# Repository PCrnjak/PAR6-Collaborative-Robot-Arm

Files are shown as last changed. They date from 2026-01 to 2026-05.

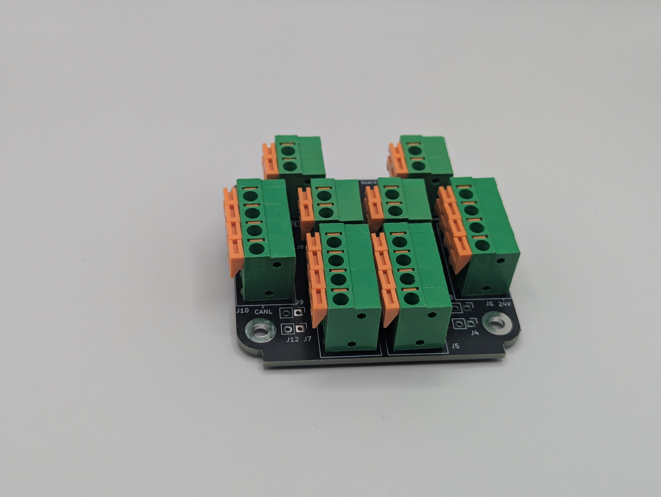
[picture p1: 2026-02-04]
BOM/BOM reference images/Base Distribution board.jpg

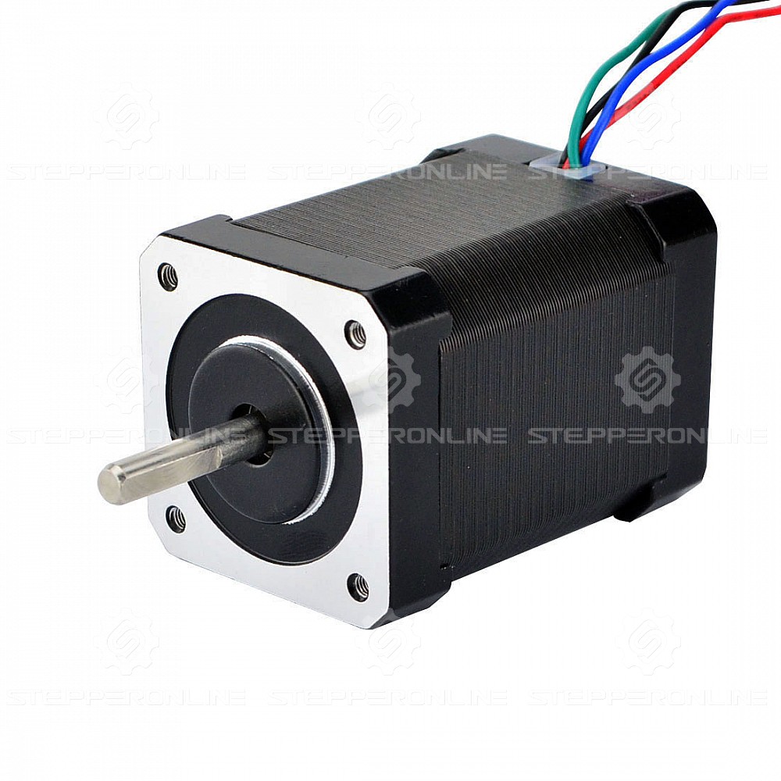
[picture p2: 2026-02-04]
BOM/BOM reference images/stepper 60mm.jpg

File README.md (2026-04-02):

> [!CAUTION]
> This is a BETA release: Instructions, code, and 3D print files may change in the future and are not yet finalized.

By building and using this system, you acknowledge that it is still under active development and may contain errors, incomplete features, or design issues. You are doing so entirely at your own risk and responsibility.

This project may require troubleshooting, modifications, and technical knowledge. Proceed only if you are comfortable working with electronics, mechanical systems, and software in a development-stage environment.
>

## 🐞 Beta Feedback

Since this project is currently in beta, feedback is highly appreciated.

If you find any mistakes, bugs, or unclear parts, please report them, including issues in:

- Documentation
- BOM and assembly documentation
- Source code
- STL and other 3D print files

Please open an issue, send us a message on Discord, or contact us via email with as much detail as possible so we can fix it quickly.

<div align="center">



# PAR6-Collaborative-Robot-Arm

</div>

---

<p align="center">
  
  
  
  <a href="https://github.com/petercorke/robotics-toolbox-python">Powered by the Robotics Toolbox</a>
  
</p>

<p align="center">
  
  
  
  
  
  
</p>

<div align="center">

3D Printed Collaborative Robot - Open Source Software, Manuals & 3D print files ·

Designed for Embodied/Physical  AI, Safety & Ease of use

</div>

## 💡 News

[2025-04-10] Test

[2025-04-03] Beta Release! Contributions from the open-source community are highly encouraged, and we welcome feedback and bug reports through the GitHub Issues page.

## 📖 Project Overview

PAR6 is a 3D-printed collaborative robot arm platform designed for research, education, and rapid prototyping in physical AI.

The project combines mechanical design files, assembly documentation, and software resources to support full-stack robotics development.

Key focus areas:

- Embodied AI and physical AI experiments and validation
- Teleoperation workflows and human-in-the-loop control
- Learning from demonstration (LfD) pipelines
- Imitation learning and dataset generation
- VLA-style data collection for AI-native robotics
- Accessible robotics research through open hardware and open documentation

## ⚒️How to build / Where to buy?

## 📚Documentation:

| Resource | Description |
|---|---|
| [3D Print Files](3D%20Print%20Files/) | Printable STL part files for the PAR6 robot arm,  |
| [BOM](BOM/) | Bill of materials and reference images for sourcing the required parts |
| [Building Instructions](Building%20Instructions/) | Assembly notes, cable building instructions, and supporting datasheets |
| [PAR6 Description](PAR6%20Description/) |  XML files, and URDF resources for simulation  |

## ⚙️ Hardware Specifications

## 🗺️ Roadmap & Status

Schedule:

| Task | Status | Description | Documentation |ETA |
| :--- | :---: | :--- | :--- | :--- |
| dsa | sad | sad | asd | asd |
---

## 🤝Get Involved

## 🌐 More about PAR6 robotic arm

| YouTube | Instagram | Twitter | LinkedIn |
|---|---|---|---|
|  |  |  |  |

| Discord | Forum | Hackaday | Blog |
|---|---|---| ---|
|  |  |  |  

## 🛡️ Licensing

CERN Open Hardware Licence Version 2 - Strongly Reciprocal

## 💸Support us

The majority of this project is open source and freely available to everyone. Your assistance, whether through donations or advice, is highly valued. Thank you!

 


## 🙌 References & Acknowledgments

## ⚠️ Safety, Liability & Disclaimer
This project includes experimental software, hardware designs, and assembly documentation that are still under development and may contain bugs, errors, or incomplete features. By using, building, or modifying this project, you acknowledge that:

* You use this project entirely at your own risk
* You are solely responsible for safe assembly, testing, and operation
* No guarantee is made regarding correctness, safety, or reliability
* The authors are not responsible for any damage, injury, or loss resulting from the use or misuse of this project
* Hardware performance and safety depend on user assembly, component quality, calibration, and handling, which cannot be guaranteed
* This project is provided “as is.” If you choose to build a device yourself using these files, designs, or instructions, you do so without any warranties or guarantees, including regarding safety, reliability, or suitability for any particular purpose.

THIS PROJECT INVOLVES LETHAL VOLTAGES AND OTHER SERIOUS HAZARDS THAT CAN CAUSE SEVERE INJURY. YOU MUST READ THE FULL [SAFETY WARNING AND DISCLAIMER DOCUMENT](SAFETY_WARNING_AND_DISCLAIMER.md)  BEFORE USING ANY PROJECT FILES. BY PROCEEDING, YOU ACKNOWLEDGE AND ACCEPT ALL RISKS AND AGREE TO USE THIS PROJECT ENTIRELY AT YOUR OWN RESPONSIBILITY.

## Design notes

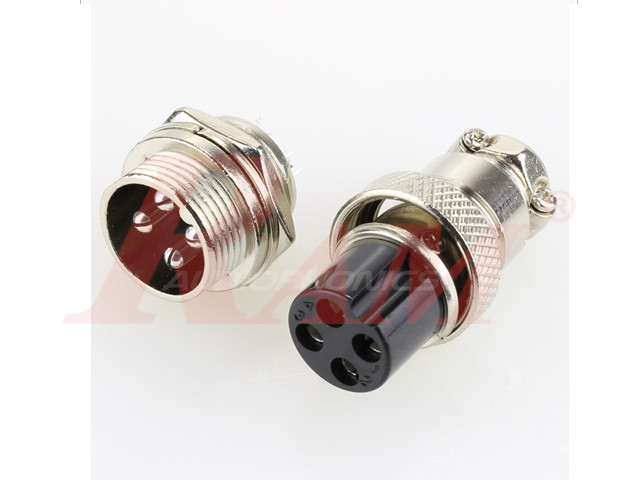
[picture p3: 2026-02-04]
BOM/BOM reference images/GX16-4 Pole Metal Male Female Panel Chassis Connector.jpg

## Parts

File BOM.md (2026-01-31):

# Gripper – Bill of Materials (BOM)

This BOM lists all components required to build the gripper. Quantities are for **one gripper**.

---

## Screws and Nuts

| Diameter / Type | Length | Quantity | Description | Link |
|---|---|---|---|---|
| M3 | 22 mm | 4 | Screw |  |
| M4 | 10 mm | 2 | Screw |  |
| M3 | 6 mm | 4 | Cheese head screw |  |
| M3 | 25 mm | 4 | Screw |  |
| M3 | 8 mm | 6 | Screw |  |
| M2 | 10 mm | 1 | Screw |  |
| M2 | 4 mm | 8 | Screw |  |
| M2.5 | 8 mm | 6 | Screw |  |
| M2 | 6 mm | 4 | Screw |  |
| M3 | 40 mm | 4 | For 17HS16-2004S1 stepper |  |
| M3 | 60 mm | 4 | For 17HS24-2104S stepper |  |

---

## Brass Inserts

| Thread | Length | Outer Diameter | Quantity | Link |
|---|---|---|---|---|
| M3 | 5 mm | 4.5 mm | 8 | [Link](https://s.click.aliexpress.com/e/_c2RX6lzp) |

---

## Motors (You need one of these per gripper!)

| Type | Quantity | Description | Link |
|---|---|---|---|
| 17HS08-1004S | 1 | 21.5mm stepper | [Link](https://www.omc-stepperonline.com/nema-17-bipolar-1-8deg-16ncm-22-6oz-in-1a-3-7v-42x42x20mm-4-wires-17hs08-1004s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)  |
| 17HS16-2004S1 | 1 | 40mm stepper  | [Link](https://www.omc-stepperonline.com/nema-17-bipolar-45ncm-64oz-in-2a-42x42x40mm-4-wires-w-1m-cable-connector-17hs16-2004s1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) |
| 17HS24-2104S | 1 | 60mm stepper | [Link](https://www.omc-stepperonline.com/nema-17-bipolar-1-8deg-65ncm-92oz-in-2-1a-3-36v-42x42x60mm-4-wires-17hs24-2104s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) |

---

## Mechanical Components

| Type | Quantity | Description | Link |
|---|---|---|---|
| Shaft coupler | 1 | 8 mm bore, M4 screw holes | [Link](https://s.click.aliexpress.com/e/_c3pkoqsb) |
| MGN7C slider | 2 | Linear guide carriage | [Link](https://s.click.aliexpress.com/e/_c4sRNxXV) |
| Linear guide | 1 | 100 mm, 150 mm and 200 length works | [Link](https://s.click.aliexpress.com/e/_c4sRNxXV) |
| Magnet | 1 | 6 mm diameter, 2.5 mm thickness | [Link](https://source-robotics.com/products/6x2-5mm-diametrical-neodymium-magnet) |
| Gear 32P 21T | 1 | | [Link](https://s.click.aliexpress.com/e/_c3oAnoc7) |
| Thermal cement | 1 | | [Link](https://s.click.aliexpress.com/e/_c3dBOwTD) |

---

## Electronics

| Type | Quantity | Description | Link |
|---|---|---|---|
| STEPFOC motor controller | 1 | Motor controller | [Link](https://source-robotics.com/products/spectral-micro-bldc-controller) |
| 100K Thermistor | 1 | NTC temperature sensor | [Link](https://source-robotics.com/products/100k-ntc-thermistor) |
| XH 2.54 mm cable | 1 | 300 mm, 2P, double-ended (24 V power) | [Link](https://s.click.aliexpress.com/e/_c3f1efET) |
| ZH 1.5 mm cable | 1 | 300 mm, 2P, double-ended (CAN bus) | [Link](https://s.click.aliexpress.com/e/_c3f1efET)  |
| Male 4-pin connector | 1 | Board connector | [Link](https://s.click.aliexpress.com/e/_c4OWHPKF) |
| OV9732 Camera | 1 | 100 Degree version | [Link](https://s.click.aliexpress.com/e/_c3WWVLjl) |

---

## Cables
Official cables from Source Robotics: [Link]()

Diy version below:

| Type | Length / Spec | Quantity | Description | Link |
|---|---|---|---|---|
| 26 AWG cable | 0.15 mm², 4-wire twisted pair | 0.4 m | ~40 cm usually sufficient | [Link](https://s.click.aliexpress.com/e/_c4m3ggwn) |
| 4-pin male wire connector | — | 1 | See reference image |[Link](https://s.click.aliexpress.com/e/_c4OWHPKF) |
| 4-pin female wire connector | — | 1 | See reference image | [Link](https://s.click.aliexpress.com/e/_c4OWHPKF) |

---

---

> **Note:** Equivalent parts from other suppliers may be used as long as specifications match.

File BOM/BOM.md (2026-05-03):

# PAROL6 – Bill of Materials (BOM)

This BOM lists all components required to build the PAR6 robot arm based on the official kiting list.

---

## RCB - Robot Control Box

TODO - Check this repository to build your Robot Control Box

---

## Screws and Nuts

| Diameter / Type | Length | Quantity | Description |
| :--- | :--- | :--- | :--- |
| M4 | 10 mm | 7 | DIN 912 / ISO 4762 (Socket head cap) 
| M3 | 8 mm | 50 | DIN 912 / ISO 4762 (Socket head cap) 
| M3 | 14 mm | 33 | DIN 912 / ISO 4762 (Socket head cap) 
| M3 | 25 mm | 4 | DIN 912 / ISO 4762 (Socket head cap) 
| M2 | 10 mm | 2 | DIN 912 / ISO 4762 (Socket head cap) 
| M2 | 4 mm | 2 | DIN 912 / ISO 4762 (Socket head cap) 
 M3 | 45 mm | 6 | DIN 912 / ISO 4762 (Socket head cap) 
  M2.5 | 14 mm | 8 | DIN 912 / ISO 4762 (Socket head cap) 
| M3 | 16 mm | 6 | DIN 912 / ISO 4762 (Socket head cap) 
| M3 | 12 mm | 3 | DIN 912 / ISO 4762 (Socket head cap) 
| M4 | 16 mm | 16 | DIN 912 / ISO 4762 (Socket head cap) 
| M4 | 14 mm | 4 | DIN 912 / ISO 4762 (Socket head cap)
| M4 | 50 mm | 4 | DIN 912 / ISO 4762 (Socket head cap)
| M3 | 15 mm or 16 | 5 | Tapered / Countersunk screw head 
| M5 | 16 mm | 8 | DIN 912 / ISO 4762 (Socket head cap)|
| M3 | 22 mm | 4 | DIN 912 / ISO 4762 (Socket head cap)|
| M3 | 40 mm | 8 | DIN 912 / ISO 4762 (Socket head cap)| 
| M3| 60 mm | 12 | DIN 912 / ISO 4762 (Socket head cap)| 

---

[Alt Link](https://s.click.aliexpress.com/e/_oEhMNU5)

## Gearboxes

| Name | Type | Quantity | Description | Link | ALT link| Reference Image |
| :--- | :--- | :--- | :--- | :--- | :--- |:--- |
| Gearbox 20:1 | Nema 17 20:1 | 2 | EG Series precision planetary | [Link](https://www.omc-stepperonline.com/eg-series-planetary-gearbox-gear-ratio-20-1-backlash-20-arc-min-for-nema-17-stepper-motor-eg17-g20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) | [Alt Link](https://s.click.aliexpress.com/e/_oEhMNU5) | [Link](BOM%20reference%20images/stepper%2020_1.jpg) |
| Gearbox 10:1 | Nema 17 10:1 | 1 | EG Series precision planetary | [Link](https://www.omc-stepperonline.com/eg-series-planetary-gearbox-gear-ratio-10-1-backlash-15-arc-min-for-nema-17-stepper-motor-eg17-g10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) | [Alt Link](https://s.click.aliexpress.com/e/_oEhMNU5) |[Link](BOM%20reference%20images/stepper%2010_1.jpg) |
| Gearbox 25:1 | Nema 17 10:1 | 1 | MGL Series precision planetary | [Link](https://www.omc-stepperonline.com/mgl-series-planetary-gearbox-gear-ratio-25-1-backlash-45arc-min-for-5mm-shaft-standard-nema-17-stepper-motor-mgl17-g25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) | [Alt Link](https://s.click.aliexpress.com/e/_c2QcIBnD) |[Link](BOM%20reference%20images/stepper%2010_1.jpg) |

25:1 Gearbox is still being tested. It might replace 20:1 used in J2!

> [!NOTE]
>     **You can use Lower quality MSG type reducers. They offer a tradeoff where they are cheaper but have more backlash**

---

## Motors

| Name | Type | Quantity | Description | Link | ALT link| Reference Image |
| :--- | :--- | :--- | :--- | :--- | :--- | :--- |
| Stepper 17HS08-1004S | Nema 17 | 1 | 16Ncm, 42x42x21.5mm; used in J6| [Link](https://www.omc-stepperonline.com/nema-17-bipolar-1-8deg-16ncm-22-6oz-in-1a-3-7v-42x42x20mm-4-wires-17hs08-1004s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) | [Alt Link](https://s.click.aliexpress.com/e/_oo1LTs7) |[Link](BOM%20reference%20images/stepper%2021_5mm.jpg) |
| Stepper 17HS16-2004S1 | Nema 17 | 2 | 45Ncm, 42x42x40mm; used in J5, J4| [Link](https://www.omc-stepperonline.com/nema-17-bipolar-45ncm-64oz-in-2a-42x42x40mm-4-wires-w-1m-cable-connector-17hs16-2004s1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) | [Alt Link](https://s.click.aliexpress.com/e/_oC1Ii0v) |[Link](BOM%20reference%20images/stepper%2040mm.jpg) |
| Stepper 17HS24-2104S | Nema 17 | 3 | 65Ncm, 42x42x60mm; used in J3, J2, J1 | [Link](https://www.omc-stepperonline.com/nema-17-bipolar-1-8deg-65ncm-92oz-in-2-1a-3-36v-42x42x60mm-4-wires-17hs24-2104s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) | [Alt Link](https://s.click.aliexpress.com/e/_opq2ugp) |[Link](BOM%20reference%20images/stepper%2060mm.jpg) |

---

## Belts and Pulleys

| Name | Type | Quantity | Description | Link | ALT link| Reference Image |
| :--- | :--- | :--- | :--- | :--- | :--- | :--- |
| Joint 1 belt | HTD3M 396 | 1 | 6 mm width | [Link](https://s.click.aliexpress.com/e/_Dn5FasX) | |[Link](BOM%20reference%20images/HTD%203M%20belt.png) |
| Joint 3 belt | HTD3M 342 | 1 | 6 mm width | [Link](https://s.click.aliexpress.com/e/_DeIf41z) | |[Link](BOM%20reference%20images/HTD%203M%20belt.png) |
| Joint 4 belt | HTD3M 201 | 1 | 6 mm width | [Link](https://s.click.aliexpress.com/e/_Dc9GUKX) | |[Link](BOM%20reference%20images/HTD%203M%20belt.png) |
| Joint 5 belt | HTD3M 246 | 1 | 6 mm width | [Link](https://s.click.aliexpress.com/e/_Dm2tHRd) | |[Link](BOM%20reference%20images/HTD%203M%20belt.png) |
| J4/J5 Pulley | HTD3M 12T | 2 | 5mm bore, 10mm width | [Link](https://s.click.aliexpress.com/e/_DBVgkVp) | |[Link](BOM%20reference%20images/HTD%203M%20pulley.png) |
| J1 Pulley | HTD3M 15T | 1 | 5mm bore, 10mm width | [Link](https://s.click.aliexpress.com/e/_DBVgkVp) | |[Link](BOM%20reference%20images/HTD%203M%20pulley.png) |

---

## Bearings and Mechanical Components

| Name | Type | Quantity | Description | Link | ALT link| Reference Image |
| :--- | :--- | :--- | :--- | :--- | :--- | :--- |
| Shaft coupler | For J2 & J3 | 2 | M2.5 screw holes | [Link](TODO) | |[Link](BOM%20reference%20images/shaft_coupler_J2_J3.png) |
| Shaft coupler | For gripper / flange | 1 | M4 screw holes | [Link](https://s.click.aliexpress.com/e/_c2xnQgI7) | |[Link](BOM%20reference%20images/shaft%20coupler%20gripper.png) |
| AXK3552 | AXK3552 needle bearing | 1 | 35X52X4, with plates | [Link](https://s.click.aliexpress.com/e/_Dk4bHg7) | |[Link](BOM%20reference%20images/AXK3552%20needle%20bearing.png) |
| NSK HR32906J| NSK HR32906J  Tapered bearing| 5 | Joint 5, 4 and 3 | [Link](https://s.click.aliexpress.com/e/_DcJMtBl) | |[Link](BOM%20reference%20images/Tapered%20bearing.png) |
| NSK HR32907J | NSK HR32907J Tapered bearing | 4 | Joint 1 and 2 | [Link](https://s.click.aliexpress.com/e/_DcJMtBl) | |[Link](BOM%20reference%20images/Tapered%20bearing.png) |
| Tensioning bearing | 3x8x4 | 2 | Ball bearing for belts | [Link](https://s.click.aliexpress.com/e/_DCjfgFV) | |[Link](BOM%20reference%20images/small%20tension%20bearings.png) |
| Tensioning bearing | 3x10x4 | 8 | Ball bearing for belts | [Link](https://s.click.aliexpress.com/e/_DlA33Af) | |[Link](BOM%20reference%20images/small%20tension%20bearings.png) |
| Brass inserts |  | 6 | M3, 5mm len, 4.5 OD| [Link](https://s.click.aliexpress.com/e/_c2RX6lzp) | |[Link](BOM%20reference%20images/brass_insert.png) |

---

> [!NOTE]
>     **There is option to use only shaft couplers used for the gripper in the whole build but they are more prone to slipping. If doint that be sure to print alternative parts located in Upper_arm STL folder**

## Electronics

| Component | Type | Quantity | Description | Link | ALT link| Reference Image |
| :--- | :--- | :--- | :--- | :--- | :--- | :--- |
| Closed loop Stepper Drivers | STEPFOC | 6 | Stepper Drivers | [Link](https://source-robotics.com/products/stepfoc-stepper-controller) | |[Link](BOM%20reference%20images/STEPFOC%20stepper%20driver.png) |
| Thermistor  | Thermistor NTC 100K 3950 | 6 | | [Link](https://source-robotics.com/products/100k-ntc-thermistor) | |[Link](BOM%20reference%20images/Thermistor.png) |
| Gripper connector PCB |  | 1 |  | [Link](TODO) | |[Link](BOM%20reference%20images/Gripper%20connector%20PCB.jpg) |
| Hall sensor PCB |  | 1 |  | [Link](TODO) | |[Link](BOM%20reference%20images/Hall%20sensor%20PCB.jpg) |
| Base Distribution PCB |  | 1 | | [Link](TODO) | |[Link](BOM%20reference%20images/Base%20Distribution%20board.jpg) |
| Robot base connector | GX16 4PIN male connector | 1 | Male + Female pair (female part is used in cable making) | [Link](https://s.click.aliexpress.com/e/_c3o4afqR) | |[Link](BOM%20reference%20images/GX16.jpg) |
| E-stop | 19mm | 1 | Emergency switch | [Link](https://s.click.aliexpress.com/e/_c3TdMLgT) | |[Link](BOM%20reference%20images/19mm%20ESTOP.png) |
| Connectors JST ZH 1.5MM 2PIN male  |  | 10 | Used to make custom cables | [Link](https://s.click.aliexpress.com/e/_c37crJFp) | |[Link](BOM%20reference%20images/Connectors%20JST%20ZH.png) |
| Connectors JST XH 2.54MM 2PIN male |  | 10 | Used to make custom cables | [Link](https://s.click.aliexpress.com/e/_c2xeSW0J) | |[Link](BOM%20reference%20images/Connectors%20JST%20XH.jpg) |
| Thermal cement |  | 1 | Used to attach thermistor to stepper motor | [Link](https://s.click.aliexpress.com/e/_c2Qk11hV) | |[Link](BOM%20reference%20images/Thermal%20cement.jpg) |

---

## Wires

| Name | Type | Quantity | Description | Link | ALT link| Reference Image |
| :--- | :--- | :--- | :--- | :--- | :--- | :--- |
| JST ZH 1.5MM 2PIN female-female 23cm |  |  | J5 motor - J6 motor  | [Link]() |
| JST XH 2.54MM 2PIN female-female 23cm |  | | J5 motor - J6 motor  | [Link]() |
| JST ZH 1.5MM 2PIN female-male 23cm | Extension wire  |  | J5 motor - J6 motor  | [Link]() |
| JST XH 2.54MM 2PIN female-male 23cm | Extension wire  | | J5 motor - J6 motor  | [Link]() |
| JST ZH 1.5MM 2PIN female-female 10cm |  |  | J5 motor - Gripper connector PCB  | [Link]() |
| JST XH 2.54MM 2PIN female-female 10cm |  | | J5 motor - Gripper connector PCB  | [Link]() |
| JST ZH 1.5MM 2PIN female-female 23cm |  |  | Gripper connector PCB - J4 wire | [Link]() |
| JST XH 2.54MM 2PIN female-female 23cm |  | | Gripper connector PCB - J4 wire | [Link]() |
| JST ZH 1.5MM 2PIN female-male 23cm | Extension wire |  | J4 wire - J4 motor  | [Link]() |
| JST XH 2.54MM 2PIN female-male 23cm | Extension wire | | J4 wire - J4 motor  | [Link]() |
| JST ZH 1.5MM 2PIN female-female 23cm |  |  | J4 motor - Extension wire base | [Link]() |
| JST XH 2.54MM 2PIN female-female 23cm |  | | J4 motor - Extension wire base  | [Link]() |
| JST ZH 1.5MM 2PIN male-bare wire 50cm |  |  | Extension wire base -  Base Distribution PCB | [Link]() |
| JST XH 2.54MM 2PIN male-bare wire 50cm |  | | Extension wire base -  Base Distribution PCB  | [Link]() |
| JST ZH 1.5MM 2PIN female-bare wire 50cm |  |  | J3 motor -  Base Distribution PCB,  | [Link]() |
| JST XH 2.54MM 2PIN female-bare wire 50cm |  | | J3 motor -  Base Distribution PCB  | [Link]() |
| JST ZH 1.5MM 2PIN female-bare wire 50cm |  |  | J2 motor -  Base Distribution PCB | [Link]() |
| JST XH 2.54MM 2PIN female-bare wire 50cm |  | | J2 motor -  Base Distribution PCB  | [Link]() |
| JST ZH 1.5MM 2PIN female-bare wire 50cm |  |  | J1 motor -  Base Distribution PCB | [Link]() |
| JST XH 2.54MM 2PIN female-bare wire 50cm |  | | J1 motor -  Base Distribution PCB  | [Link]() |
| JST ZH 1.5MM 2PIN female-bare wire 10cm |  |  |  GX16 connector -  Base Distribution PCB | [Link]() |
| JST XH 2.54MM 2PIN female-bare wire 10cm |  | | GX16 connector -  Base Distribution PCB  | [Link]() |
| Thin wire 3 colors 20 cm |  | | Hall sensor PCB - J6 motor  | [Link]() |

---

> [!IMPORTANT]
>     **Cable building guide is [here](.\Building%20instruction\Building_cables.md)**

> [!IMPORTANT]
>     **If you dont want to build the cables yourself you can get the cable pack from our store**

---

## Electric Gripper options

Default end effector is basic flange. That part can be used to attach any other custom grippers.

Officially supported open-source grippers are:

| Name | Type | Link to buy | Link to build |
| :--- | :--- | :--- | :--- |
MSG compliant AI gripper | Electric - CAN bus comms|  [Link](TODO)  | [Link](TODO)  |
SSG48 compliant gripper | Electric - CAN bus comms|  [Link](TODO) | [Link](TODO)  |

> [!NOTE]
>     **MSG gripper come in different grip and torque sizes!**

---

## MSG & SSG48 gripper cable

Buy Official cables from Source Robotics: [Link](TODO)

Parts needed if DIY your own cable:

| Type | Length / Spec | Quantity | Description | Link |
|---|---|---|---|---|
| 26 AWG cable | 0.15 mm², 4-wire twisted pair | 0.4 m | ~40 cm usually sufficient | [Link](https://s.click.aliexpress.com/e/_c4m3ggwn) |
| M8 4-pin male wire connector | — | 1 | [See reference image](../BOM/BOM%20reference%20images/M8%20male.png) |[Link](https://s.click.aliexpress.com/e/_c4OWHPKF) |
| M8 4-pin female wire connector | — | 1 | [See reference image](../BOM/BOM%20reference%20images/M8_female.png) | [Link](https://s.click.aliexpress.com/e/_c4OWHPKF) |

> [!NOTE]
>     **PAROL6 and PAR6 use different cables for SSG48 and MSG grippers. Using incorrect one can damage your robot**

## Pneumatics (optional)

> [!NOTE]
>     **These are the items we recommend if you are going to use Pneumatics with PAR6.**

| Name | Type | Quantity | Description | Link | ALT link| Reference Image |
| :--- | :--- | :--- | :--- | :--- | :--- | :--- |
| MHZ2-16D gripper | 4mm PM | 1 | Robot side connector | [Link](https://s.click.aliexpress.com/e/_DD83OLZ) |
| Pneumatic Tube |  |2 meter, 4x2.5mm | Polyurethane tube | [Link](https://s.click.aliexpress.com/e/_DEhvFyJ) |
| Solenoid valve | 4mm tube connectors, 5/2, 24V | 1 | Polyurethane tube | [Link](https://s.click.aliexpress.com/e/_DDrw0Ux) |

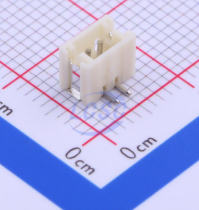
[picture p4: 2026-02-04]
BOM/BOM reference images/Connectors JST ZH 1.5MM 2PIN.png

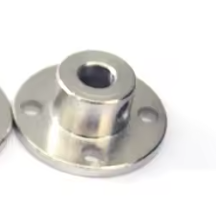
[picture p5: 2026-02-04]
BOM/BOM reference images/shaft coupler gripper.png

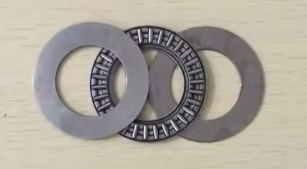
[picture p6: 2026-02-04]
BOM/BOM reference images/AXK3552 needle bearing.png

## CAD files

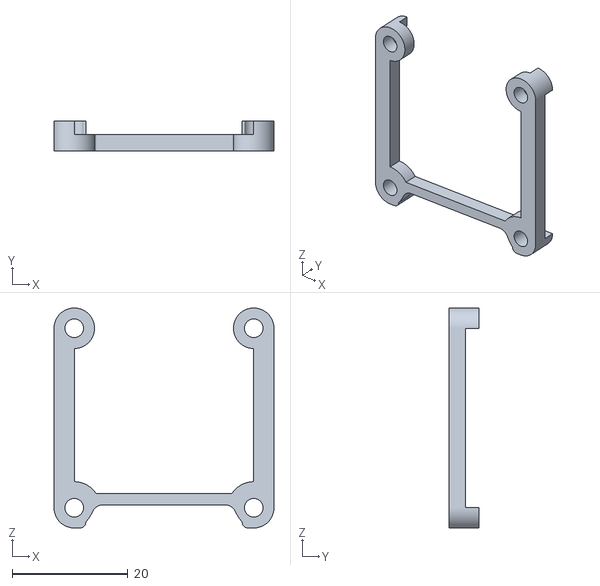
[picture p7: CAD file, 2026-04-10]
3D Print Files/STL/A1_Wrist/Stepper_spacer_J6.STL
38.0 x 5.15 x 38.0

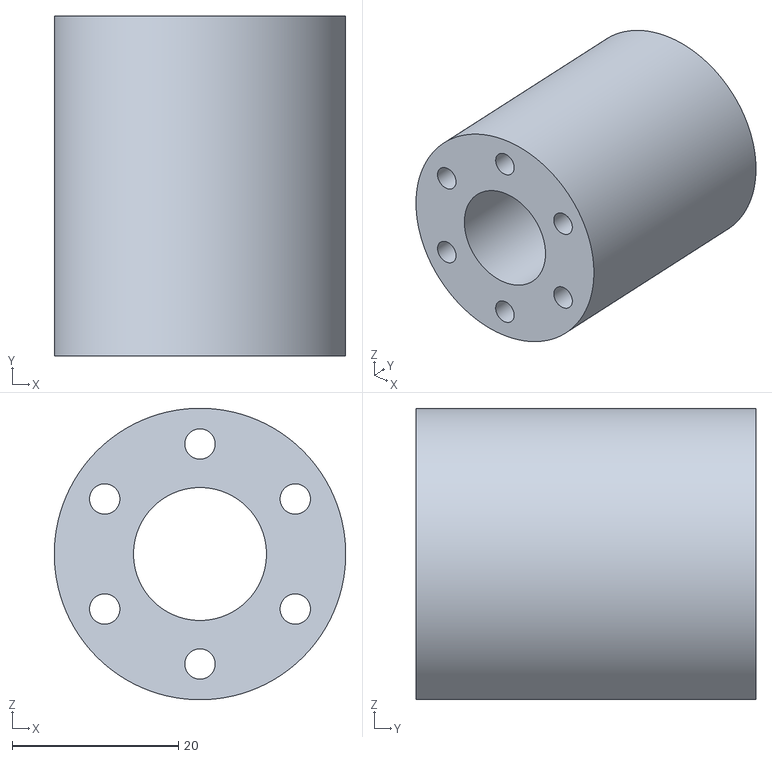
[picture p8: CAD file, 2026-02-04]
3D print files/STL/Base/J1_rotation_shaft.STL
35.1 x 41.0 x 35.1

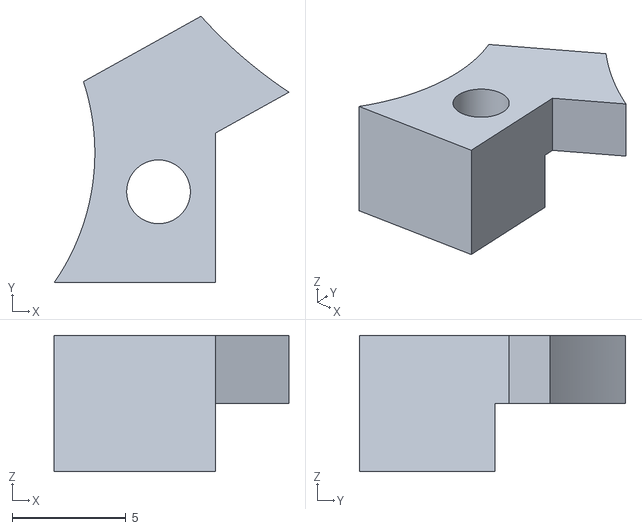
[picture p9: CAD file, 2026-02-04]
3D print files/STL/Elbow/J4_limiter.STL
10.3 x 11.7 x 6.00

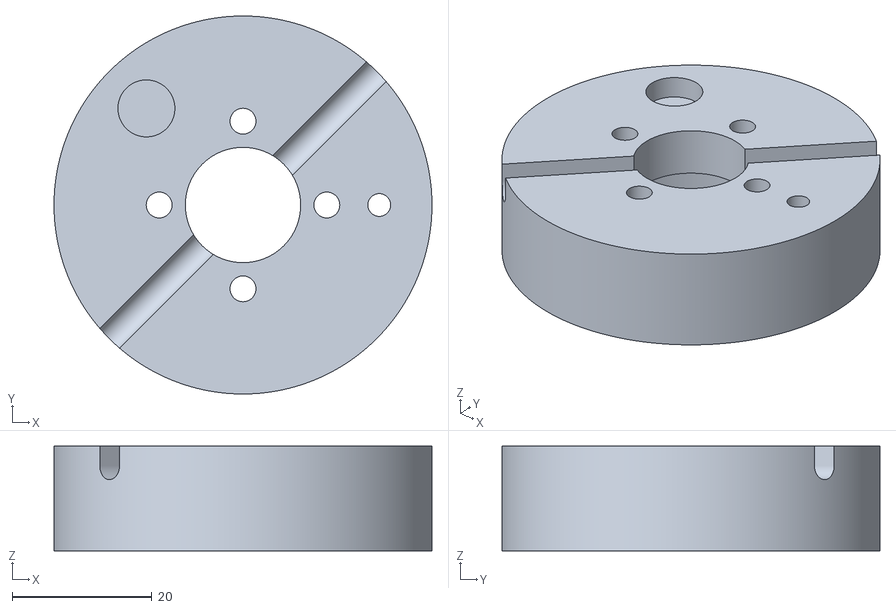
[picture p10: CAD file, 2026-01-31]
3D print files/STL/End_effector/PAR6_flange.STL
54.1 x 54.1 x 15.0

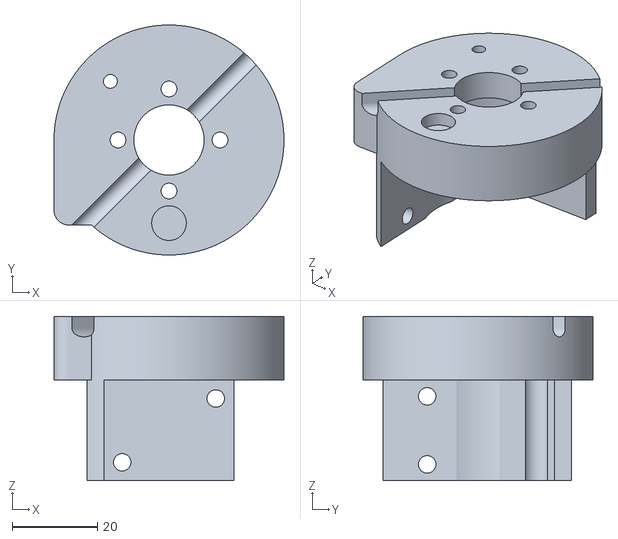
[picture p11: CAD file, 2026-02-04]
3D print files/STL/End_effector/Pneumatic grippers/Pneumatic_gripper_holder_MHZ2-16D.STL
54.1 x 54.1 x 38.6

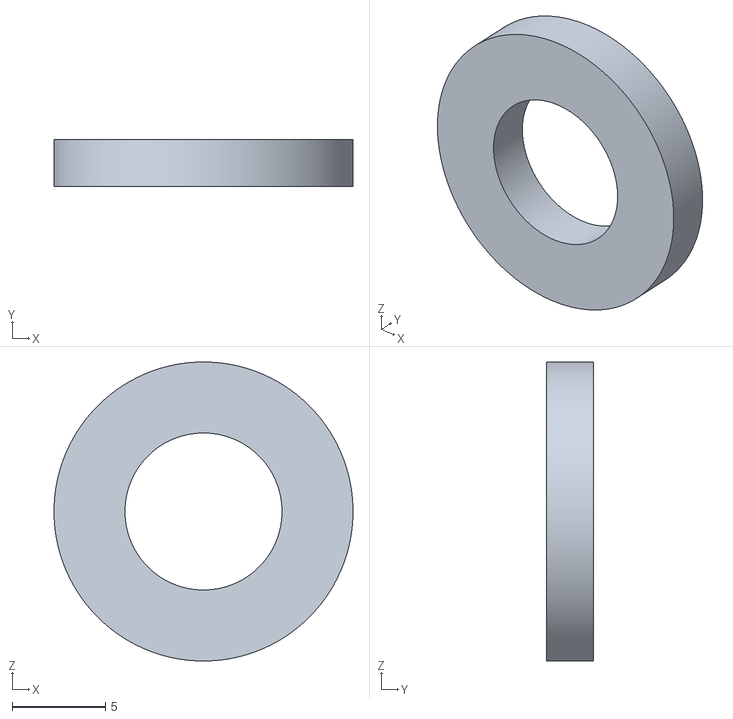
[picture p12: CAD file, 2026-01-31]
3D print files/STL/End_effector/SSG48 gripper needed parts/SSG48_gripper_spacer.STL
16.0 x 2.50 x 16.0

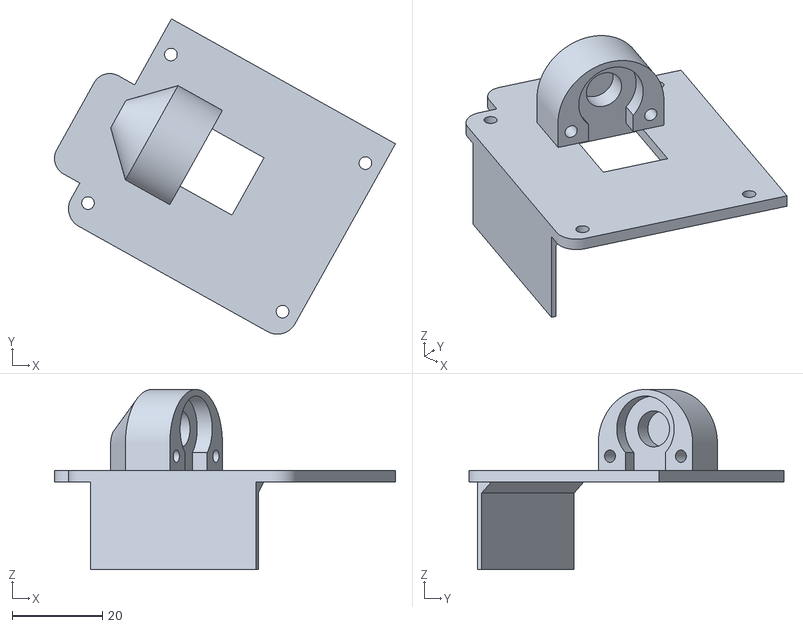
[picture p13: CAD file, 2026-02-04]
3D print files/STL/Lower_arm/electronics_lid_lower_arm_connector.STL
75.8 x 70.1 x 40.0

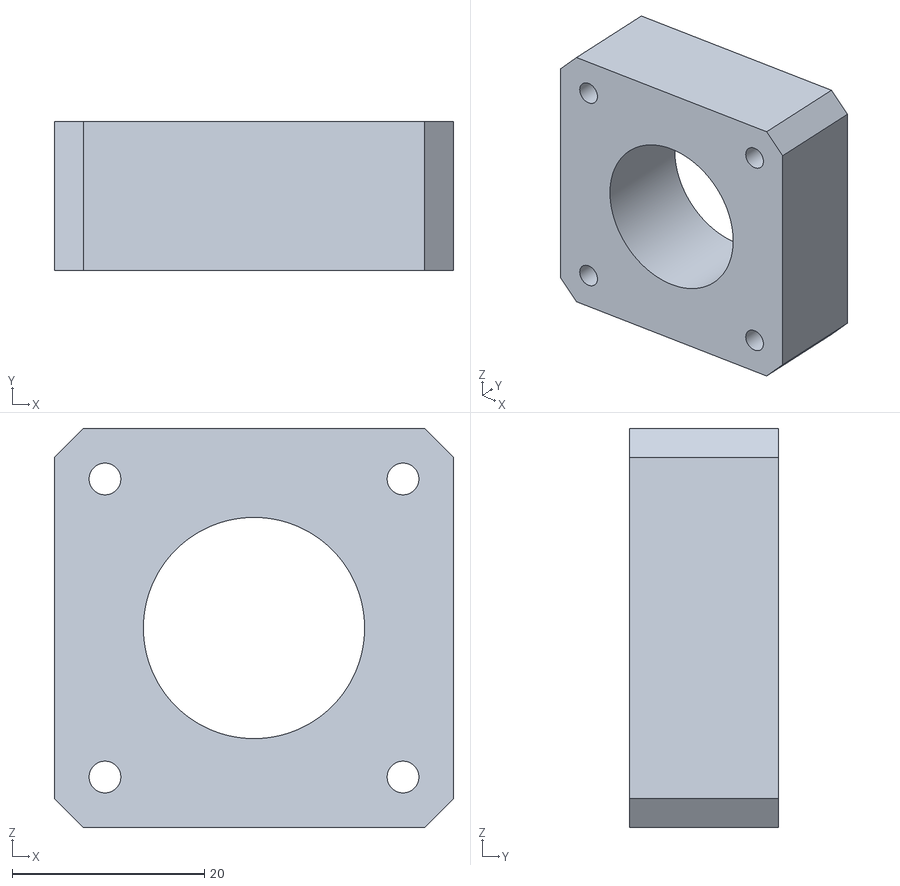
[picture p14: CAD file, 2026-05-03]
3D Print Files/STL/Miscellaneous/MG_series_gaerbox_extender_20_1.STL
41.5 x 15.5 x 41.5

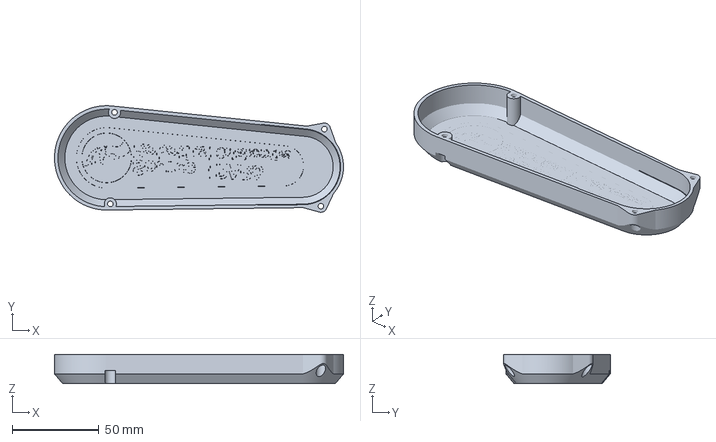
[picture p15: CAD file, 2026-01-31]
3D print files/STL/Multicolor prints/Upper_arm_cover/Upper_arm_cover_LOGO_latest.3mf
166.1 x 61.3 x 16.7 mm

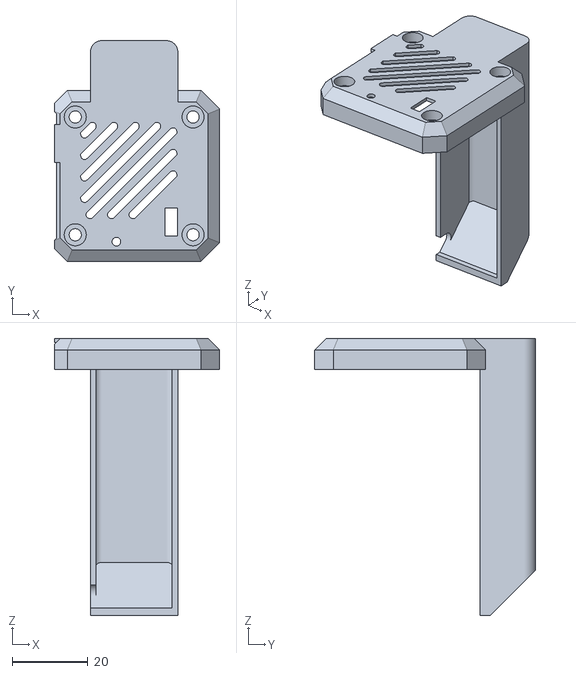
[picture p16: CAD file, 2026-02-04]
3D print files/STL/Shoulder/stepper_lid_J1.STL
43.5 x 58.1 x 72.9

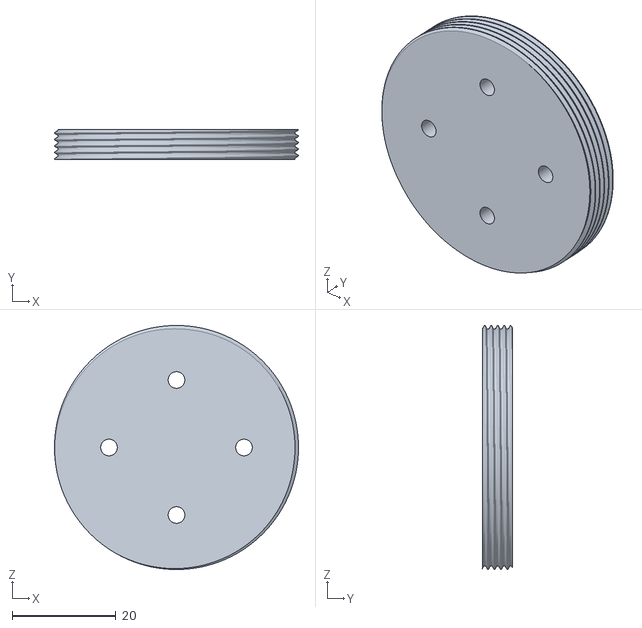
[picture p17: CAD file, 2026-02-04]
3D print files/STL/Upper_arm/J2_bearing_backplate.STL
47.0 x 5.80 x 47.0

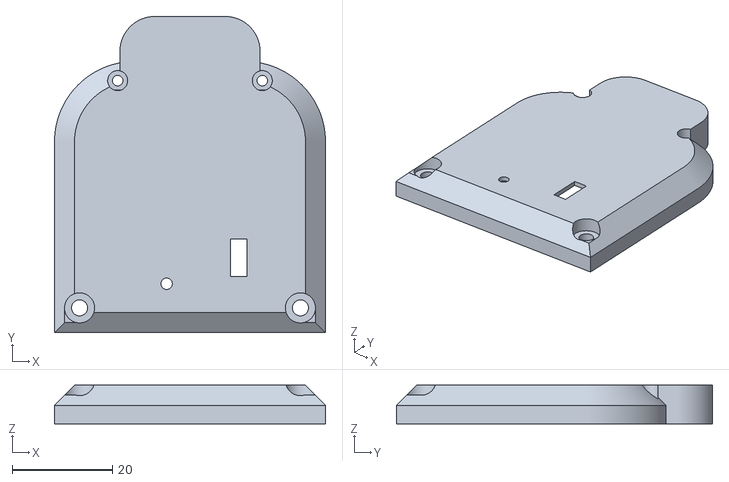
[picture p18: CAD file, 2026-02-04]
3D print files/STL/Wrist/Wrist_lid.STL
54.1 x 63.1 x 7.70

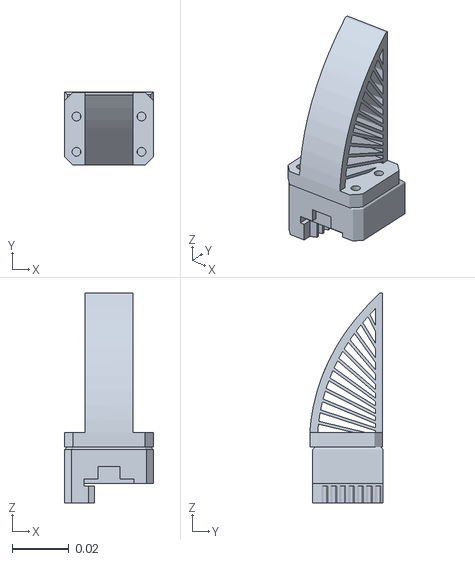
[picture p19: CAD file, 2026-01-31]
MJCF/Mujoco_model/Fin_ray_jaws/jaw1.STL
0.0314 x 0.026 x 0.0743

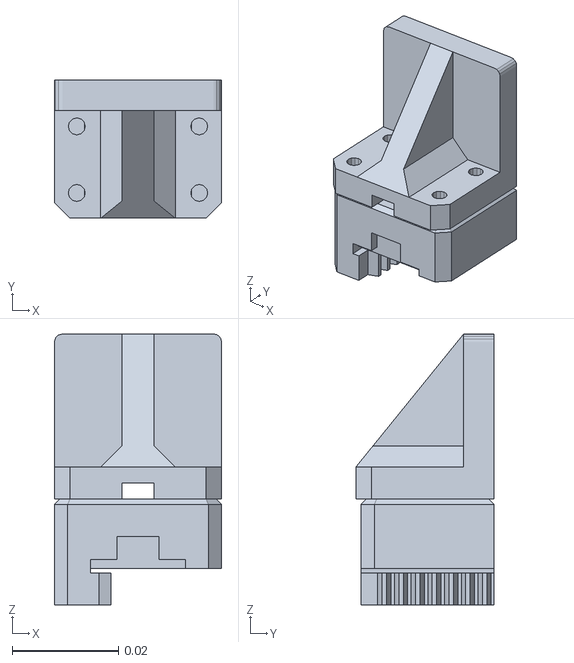
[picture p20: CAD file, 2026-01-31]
MJCF/Mujoco_model/Solid_jaws/jaw1.STL
0.0314 x 0.026 x 0.0509

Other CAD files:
3D print files/STL/Multicolor prints/J5_LID/J5_belt_lid_multicolor.gcode.3mf
3D Print Files/STL/Stepper motor accessories/MG_series_gaerbox_extender_20_1.STEP
MJCF/Mujoco_model/jaw2.STL
MJCF/Mujoco_model/solid_jaws_pinch/jaw2.STL
3D Print Files/STL/Miscellaneous/Cable_tie_mount.STL
3D Print Files/STL/Stepper motor accessories/MG_series_gearbox_extender_10_1.STL
3D Print Files/STL/Stepper motor accessories/Stepper_spacer_NEMA17.STEP
3D print files/STL/Base/Base_bearing_backplate.STL
3D print files/STL/Base/J1_bottom_lid.STL
3D print files/STL/Base/base_lid_electronics.STL
3D print files/STL/Lower_arm/J4_bearing_backplate.STL
3D print files/STL/Lower_arm/electronics_lid_lower_arm_basic.STL
3D print files/STL/Lower_arm/electronics_lid_lower_arm_connector_cover.STL
3D print files/STL/Multicolor prints/J5_LID/J5_belt_lid_multicolor.3mf
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

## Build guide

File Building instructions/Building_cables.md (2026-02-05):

# PAR6 cables

PAR6 robotic arm uses 2 types of cables:
* JST XH series for power delivery to motor drivers - 24 AWG or 22 AWG
* JST ZH series for CAN comms between motor drivers - 28 AWG

> [!IMPORTANT]
>     **It is recommended to twist all CAN bus cables**

If you want to build your own cables this document will provide you with a quick guide on how to build them.

Watch this video on cable assembly

## Building XH series extension cables

Parts needed:
* XH male connector
* XH female-female wire
* Heat shrink tube

Cut one end of the XH female-female wire and keep the wire length at around 23cm.
Place heat shrink on the wires. Solder male XH connector to the wires follow the orientations on the image below. Heat the heat shrink tubes.



## Building ZH series extension cables

Parts needed:
* ZH male connector
* ZH female-female wire
* Heat shrink tube

Cut one end of the ZH female-female wire and keep the wire length at around 23cm.
Place heat shrink on the wires. Solder male ZH connector to the wires follow the orientations on the image below. Heat the heat shrink tubes.



## Building Motor to Base Distribution PCB wire

Parts needed:
* ZH female-female wire

Cut one end of the wire and keep the length of the wire at around 50cm.

## Building Extension wire base -  Base Distribution PCB

Parts needed:
* XH male connector
* ZH male connector
* Bare wires (2 colors black and white 24 AWG)

Solder connectors based on the image below.

## Robot to Source Control Box Cable

Parts needed:
* 2 x GX16 4PIN
*  Twisted Pair Shielded Cable 4 cores - 24AWG or 22AWG
Link - https://s.click.aliexpress.com/e/_c34NcZIT

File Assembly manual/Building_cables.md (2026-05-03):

# PAR6 cables

PAR6 robotic arm uses 2 types of cables:
* JST XH series for power delivery to motor drivers - 24 AWG or 22 AWG
* JST ZH series for CAN comms between motor drivers - 28 AWG

> [!NOTE]
>     **It is recommended to twist all CAN bus cables**

> [!WARRNING]
>     **If you are unsure if cables you bought from 3rd party stores are good orientation, lenght or type we recommended buying them from our store. Using wrong cables will damage and destroy your robot.**

If you want to build your own cables this document will provide you with a quick guide on how to build them.

Watch this video on cable assembly

## XH & ZH dual female head cables
These cables need to follow the **wiring diagram** (How wires are connected to the head) shown below! 



These cables can be bought from multiple stores in different sizes.
Sizes we need for PAR6 are:
* 2 x 10cm XH dual female head/plug connector
* 2 x 10cm ZH dual female head/plug connector

* x x 23cm (difficult size to find use 25 or 30)

## XH series extension cables

Parts needed:
* XH male connector
* XH female - female wire (or female - bare wire)
* Heat shrink tube

Cut one end of the XH female-female wire and keep the wire length at around 23cm.
Place heat shrink on the wires. Solder male XH connector to the wires. Follow the orientations on the image below. Heat the heat shrink tubes.



## ZH series extension cables

Parts needed:
* ZH male connector
* ZH female - female wire (or female - bare wire)
* Heat shrink tube

Cut one end of the ZH female-female wire and keep the wire length at around 23cm.
Place heat shrink on the wires. Solder male ZH connector to the wires. Follow the orientations on the image below. Heat the heat shrink tubes.



## Motor to Base Distribution PCB wire

These wires have a female head on one side and bare wires on the another. They connect directly to the Base Distribution PCB.

Parts needed:
* ZH female-female wire or female - bare wire 

Cut one end of the wire and keep the length of the wire at around **50cm**.

## Extension wire base -  Base Distribution PCB

These wires have a male head connector on one side and bare wires on the another. They connect directly to the Base Distribution PCB.

Parts needed:
* XH male connector
* ZH male connector
* Bare wires (2 colors black and white 24 AWG)

Solder male connectors the same way as when building ZH or XH extenstion cables. 

## PAR6 Robot cable (Robot base to RCB (Robot Control Box) cable)

Parts needed:
* [2 x GX16 4PIN connector female](https://s.click.aliexpress.com/e/_c3o4afqR)
* [Twisted Pair Shielded Cable 4 cores - 24AWG or 22AWG](https://s.click.aliexpress.com/e/_c34NcZIT)

Check the video tutorial [here](TODO)



**Dissasemble the connector.**



**Connector has numbering on both sides.** 



**When assembling the cable you solder pins 1-1, 2-2, 3-3, 4-4. Do that for the both sides of the cable!** 

> [!NOTE]
>     **Pins 1-4 need to be one wisted wire pair and pins 2-3 need to be another pair!**

## Robot base connector



On the robot arm side and Robot Control Box side the we use this pinout for X16 male connector!

Solder XH wire to the pins 1 and 4. Solder ZH CAN wires to pints 3 and 2. Keep wire length at around 10cm

## MSG & SSG48 gripper cable

Buy Official cables from Source Robotics: [Link](TODO)

Parts needed if DIY your own cable:

| Type | Length / Spec | Quantity | Description | Link |
|---|---|---|---|---|
| 26 AWG cable | 0.15 mm², 4-wire twisted pair | 0.4 m | ~40 cm usually sufficient | [Link](https://s.click.aliexpress.com/e/_c4m3ggwn) |
| M8 4-pin male wire connector | — | 1 | [See reference image](../BOM/BOM%20reference%20images/M8%20male.png) |[Link](https://s.click.aliexpress.com/e/_c4OWHPKF) |
| M8 4-pin female wire connector | — | 1 | [See reference image](../BOM/BOM%20reference%20images/M8_female.png) | [Link](https://s.click.aliexpress.com/e/_c4OWHPKF) |

> [!NOTE]
>     **PAROL6 and PAR6 use different cables for SSG48 and MSG grippers. Using incorrect one can damage your robot**



End result of this cable assembly needs to look like this:



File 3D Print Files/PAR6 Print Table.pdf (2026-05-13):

We used a Prusa MK4 with the default Prusament PETG filament profile. To ensure your PAR6 robot functions properly, please try to match these print settings on your own printer. While the mass doesn't need to be exact for every part, you should aim for the values listed in the table once your model is sliced. Note: Make sure to deduct the mass of any support

### material! Mass in the table is for the parts without any support material!

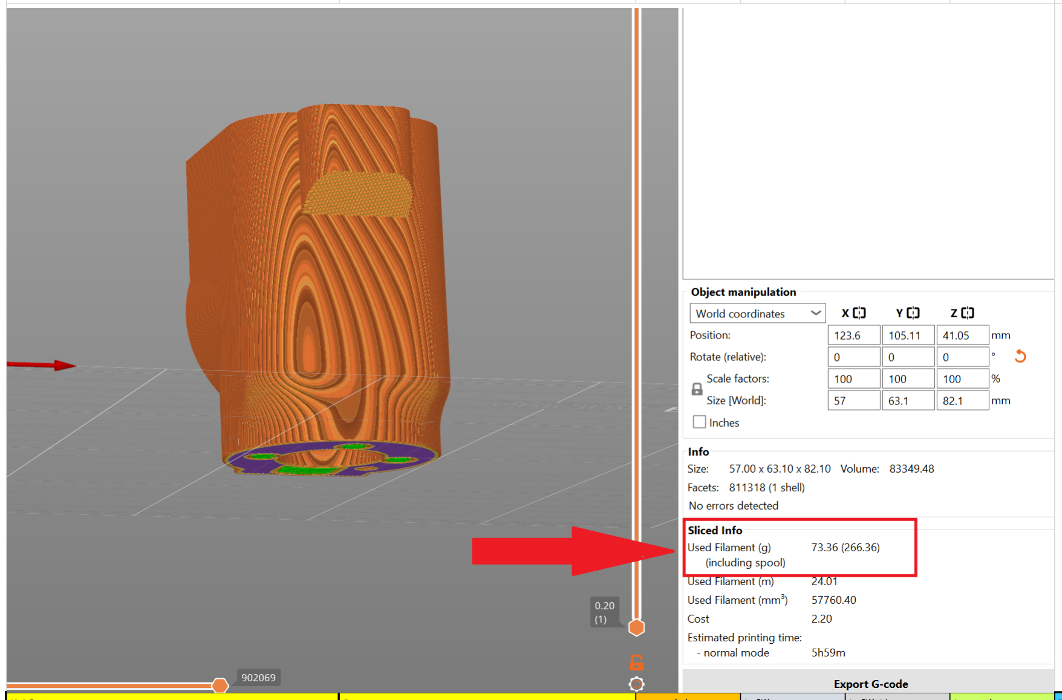
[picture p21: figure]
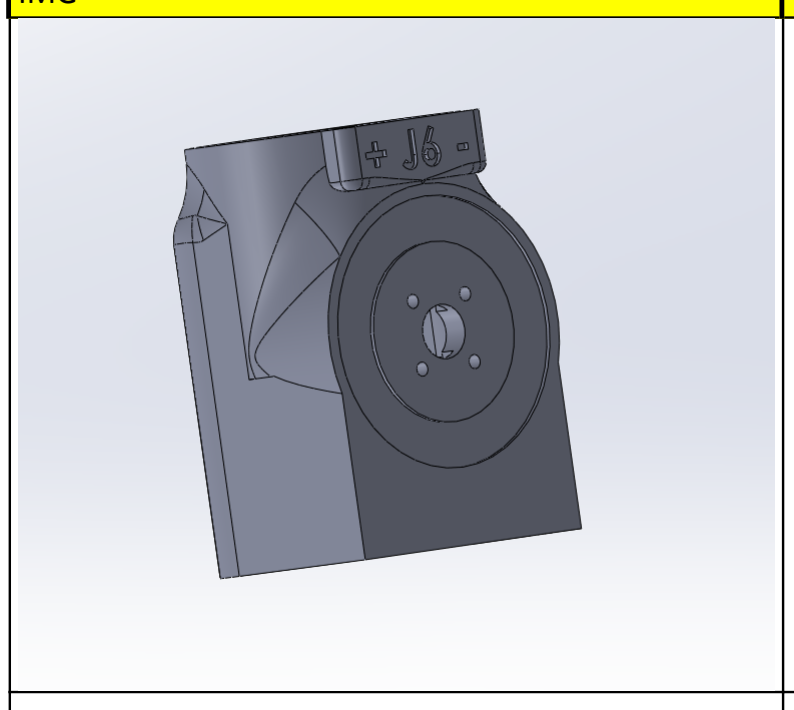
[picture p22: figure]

IMG | Part name | mass (g) | Infill type | Infill % | Layer h | Top layers | Bot layers | Perimeters
| Wrist | 70 | honey | 25 | 0.15 | 6 | 5 | 3

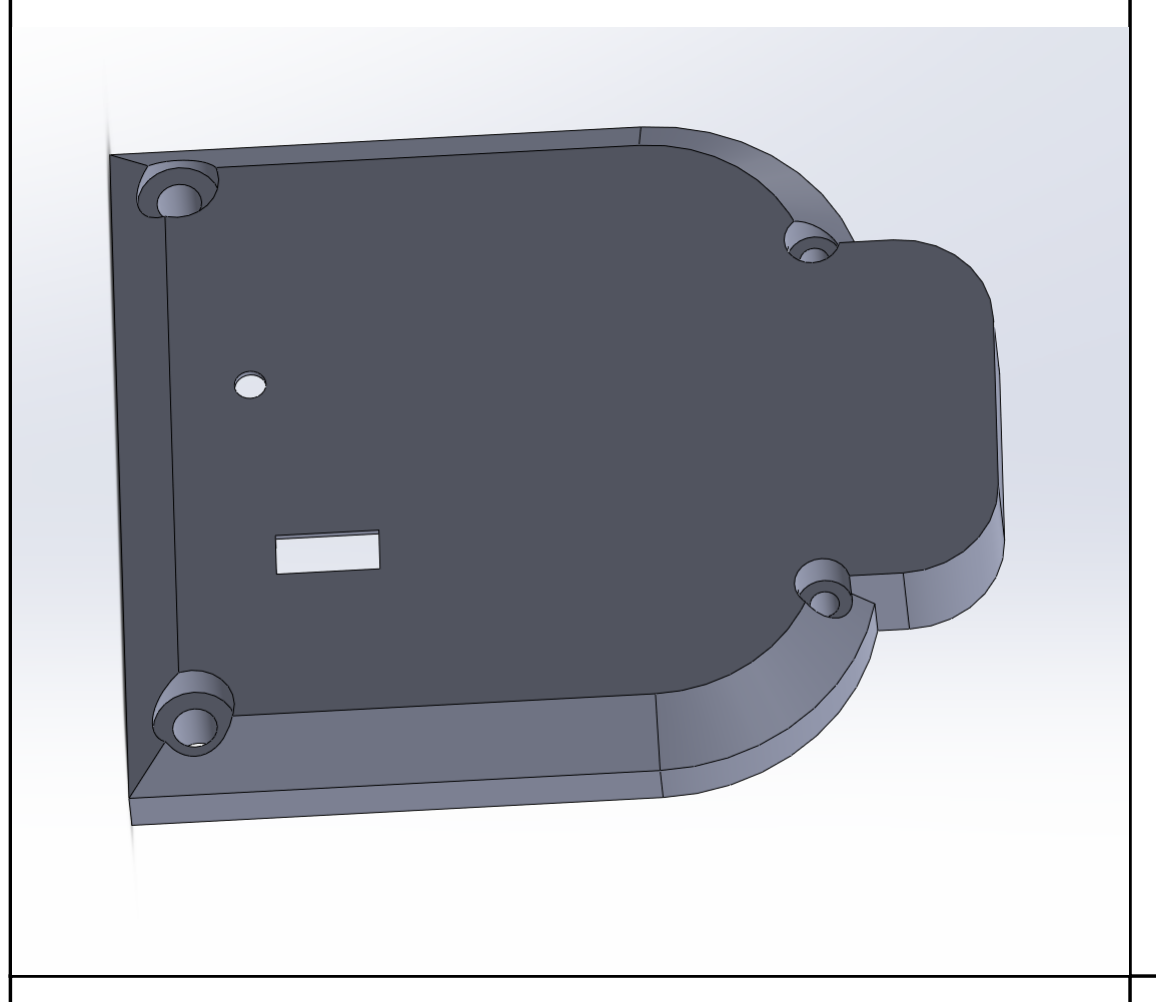
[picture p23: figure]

| Wrist lid | 8.3 | honey | 25 | 0.15 | 6 | 5 | 3

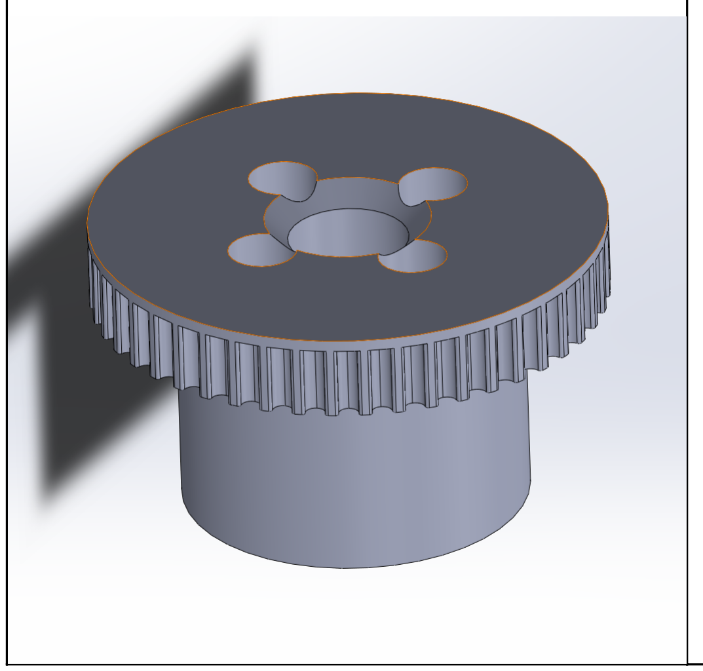
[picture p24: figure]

| Wrist pulley | 19.8 | honey | 50 | 0.15 | 6 | 5 | 3

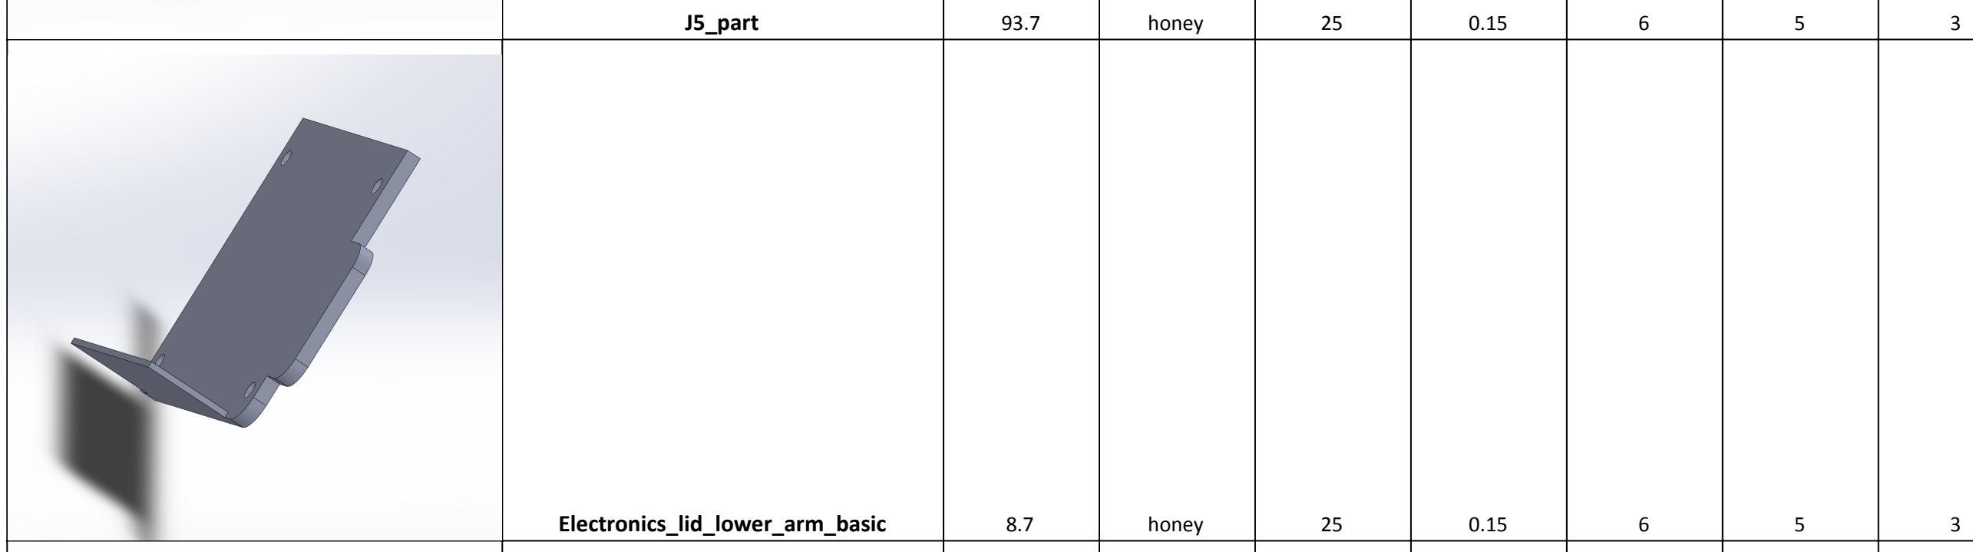
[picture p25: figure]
J5_part; honey; Electronics_lid_lower_arm_basic
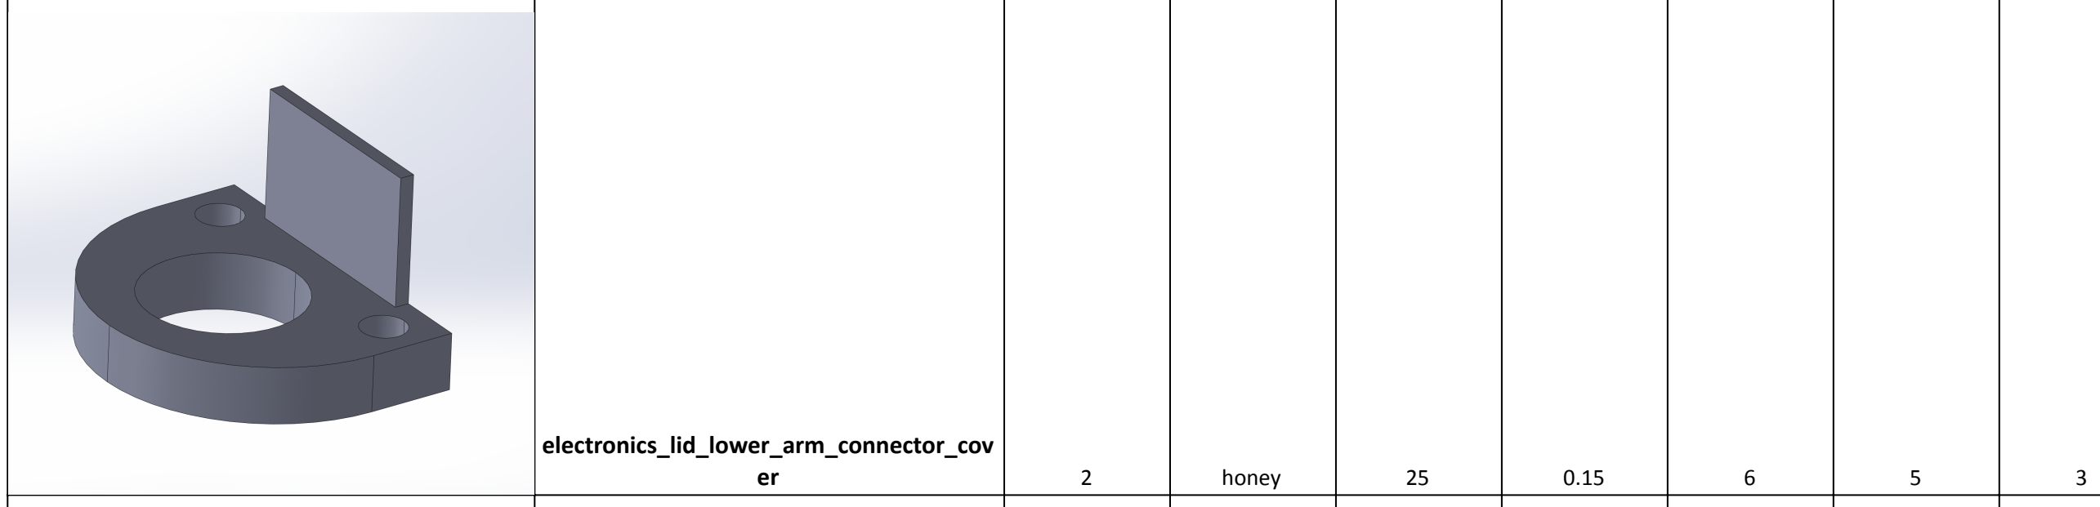
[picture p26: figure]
electronics_lid_lower_arm_connector_cov er; honey
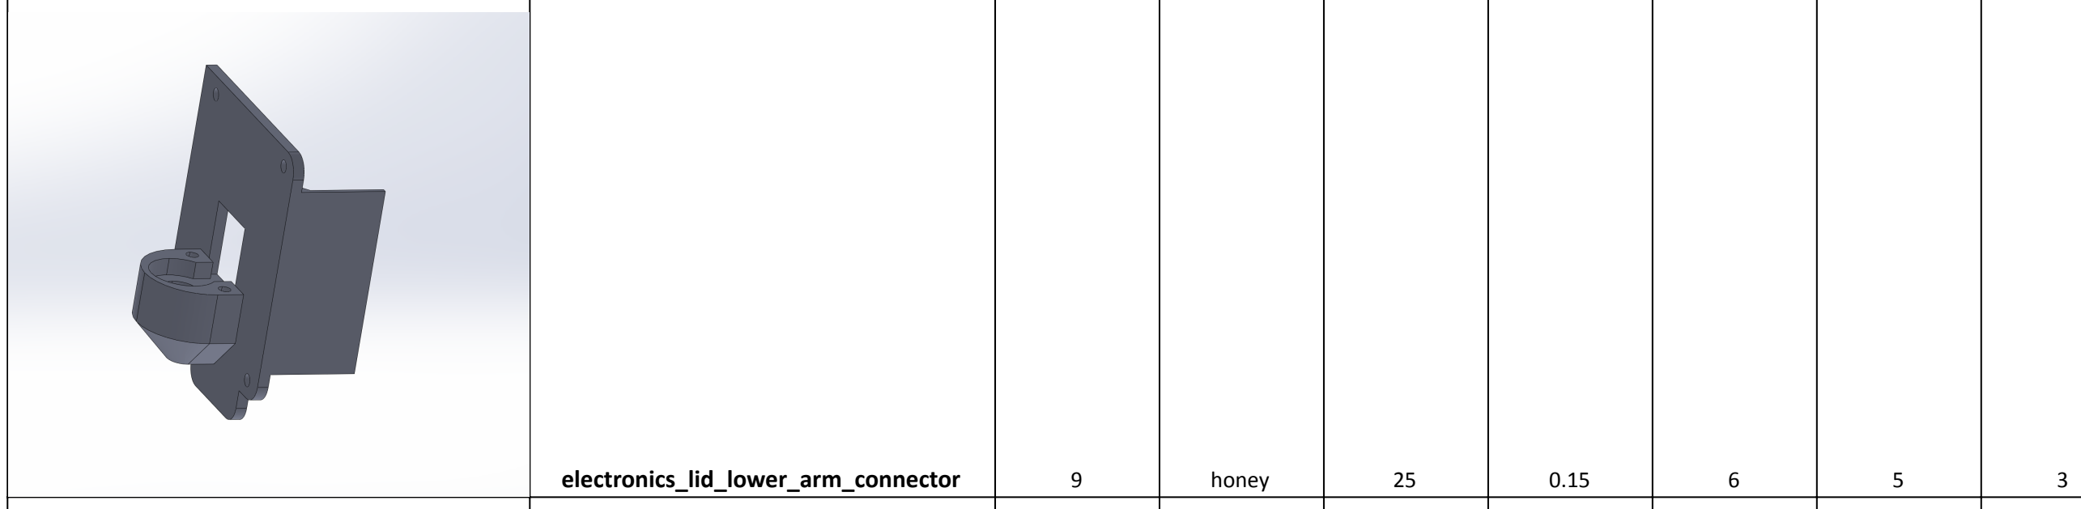
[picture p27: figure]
electronics_lid_lower_arm_connector; honey
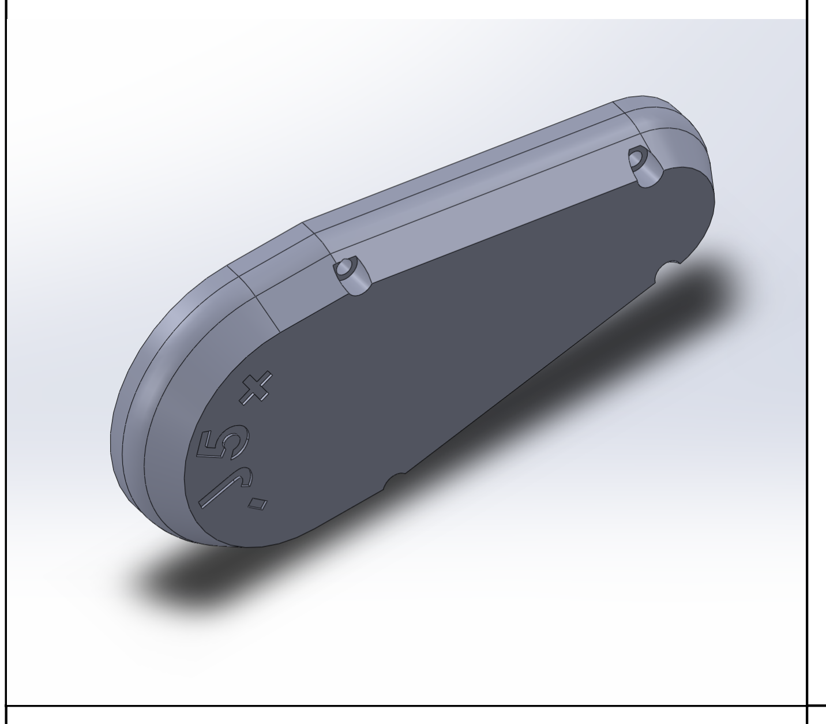
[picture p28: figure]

J5_belt_lid | 17.6 | honey | 25 | 0.15 | 6 | 5 | 3

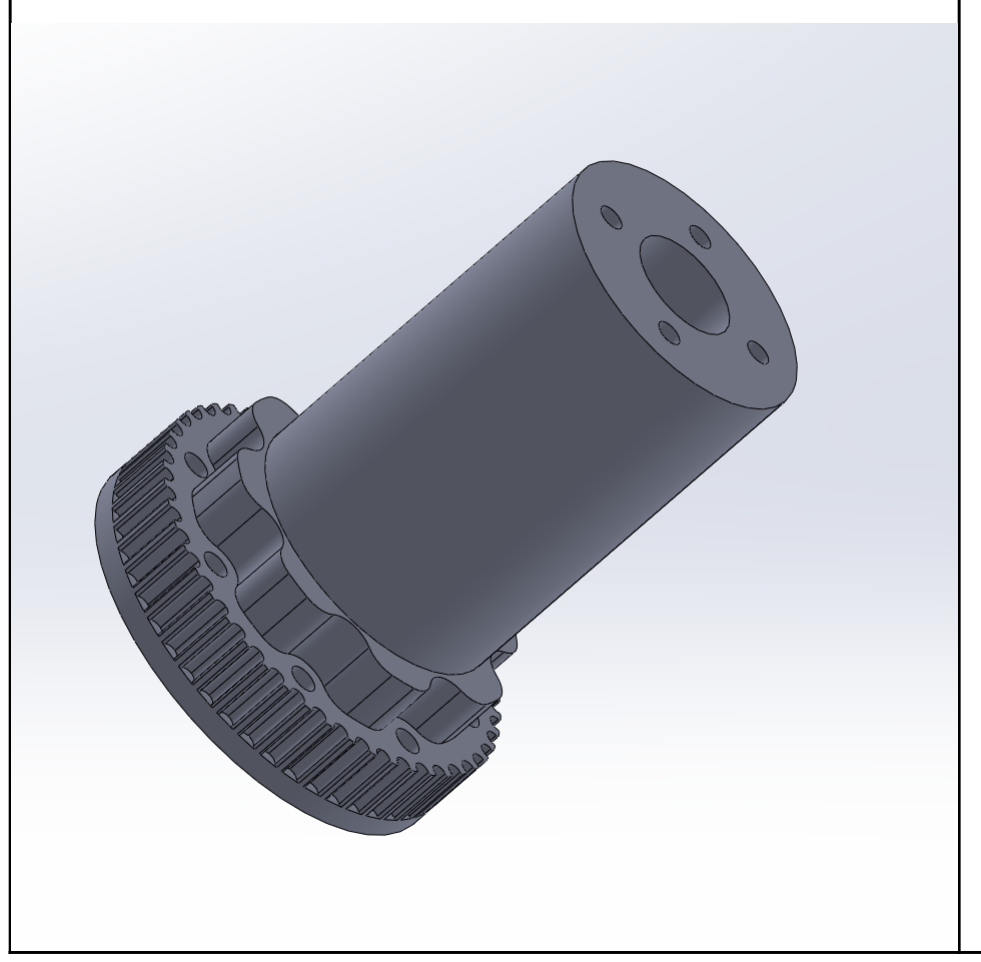
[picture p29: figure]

J4_output_pulley | 40.7 | honey | 50 | 0.15 | 6 | 5 | 3

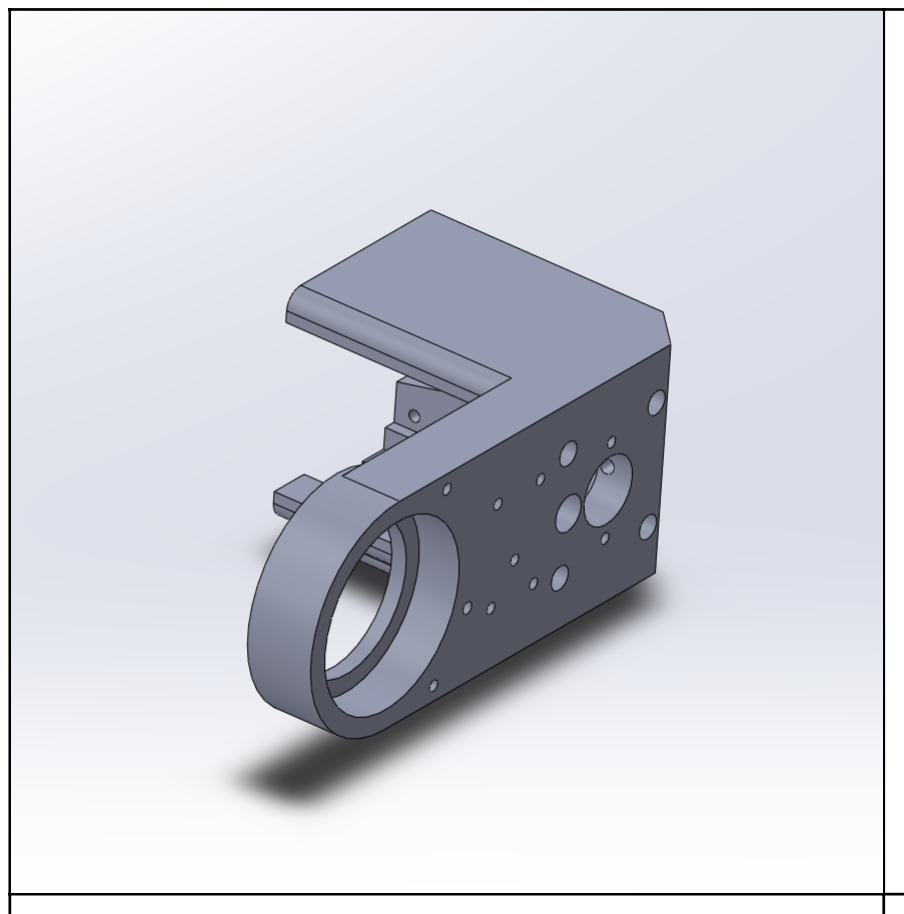
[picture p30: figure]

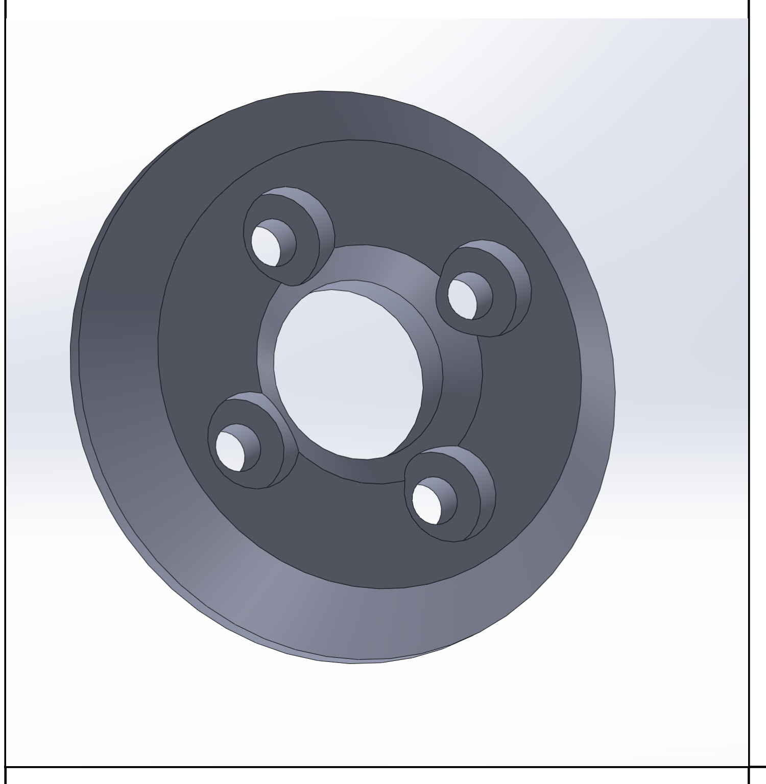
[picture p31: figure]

J4_bearing_backplate | 4 | honey | 25 | 0.15 | 6 | 5 | 3

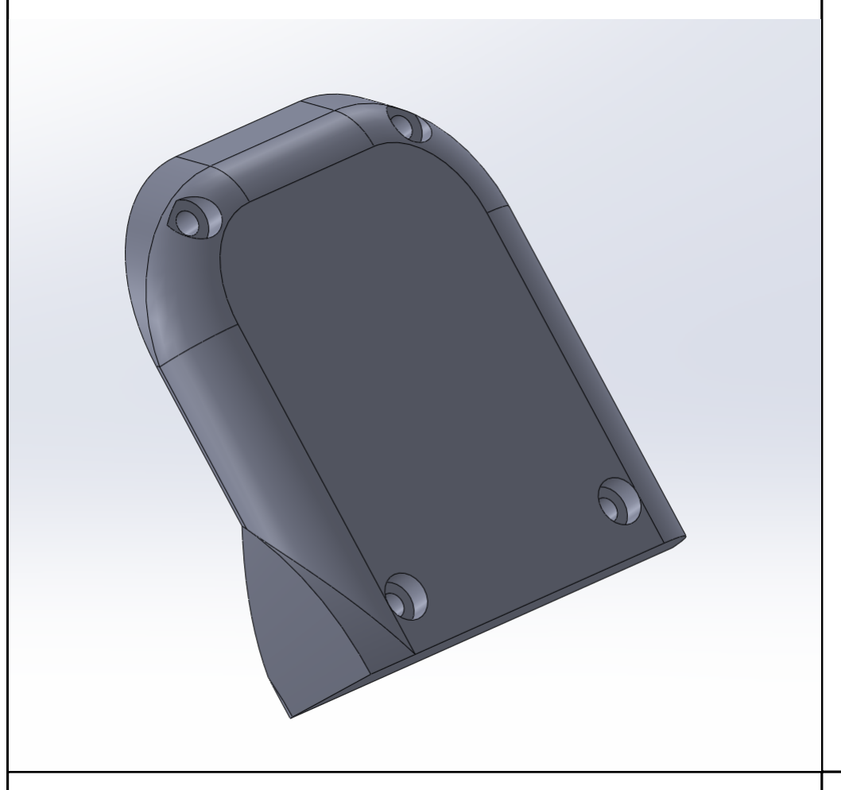
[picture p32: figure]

Elbow_lid | 19.7 | honey | 25 | 0.15 | 6 | 5 | 3

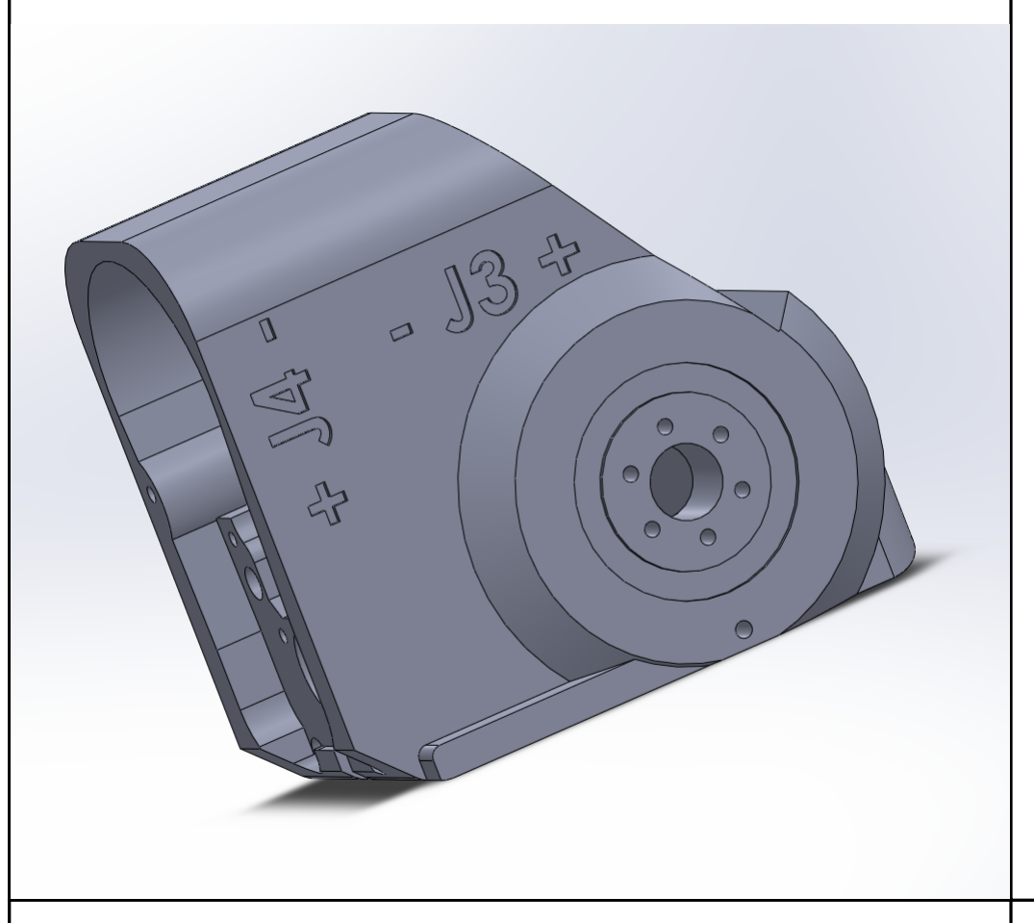
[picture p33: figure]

Elbow_part | 172.8 | honey | 25 | 0.15 | 6 | 5 | 3

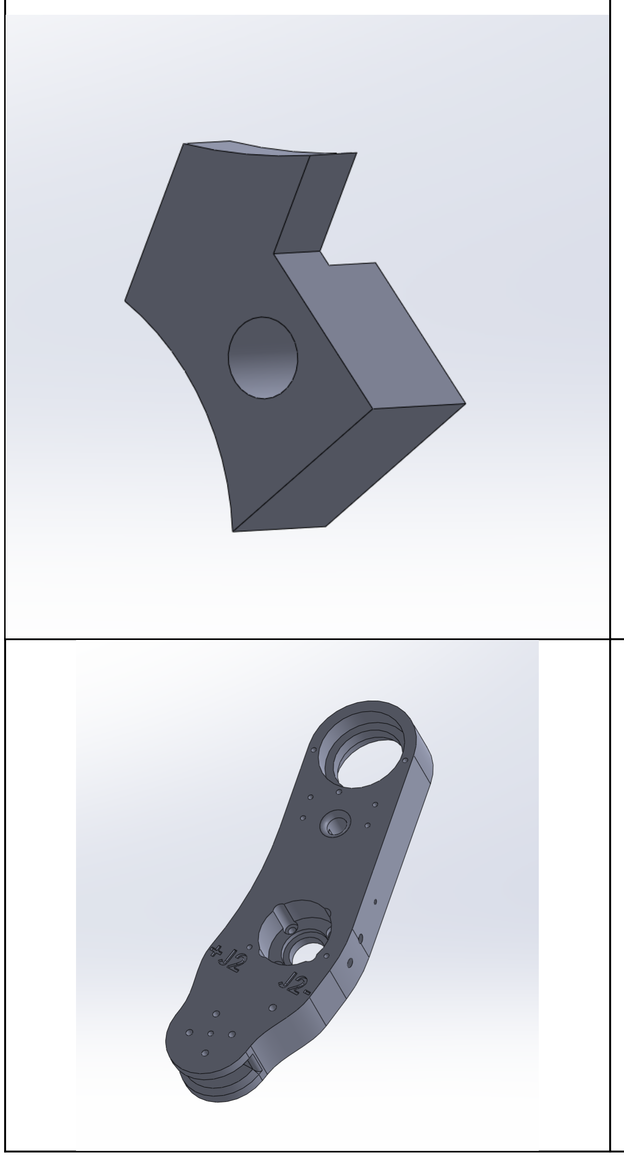
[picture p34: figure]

J4_limiter | 1 | honey | 25 | 0.15 | 6 | 5 | 3
upper_arm | 192.6 | honey | 35 | 0.15 | 6 | 5 | 3

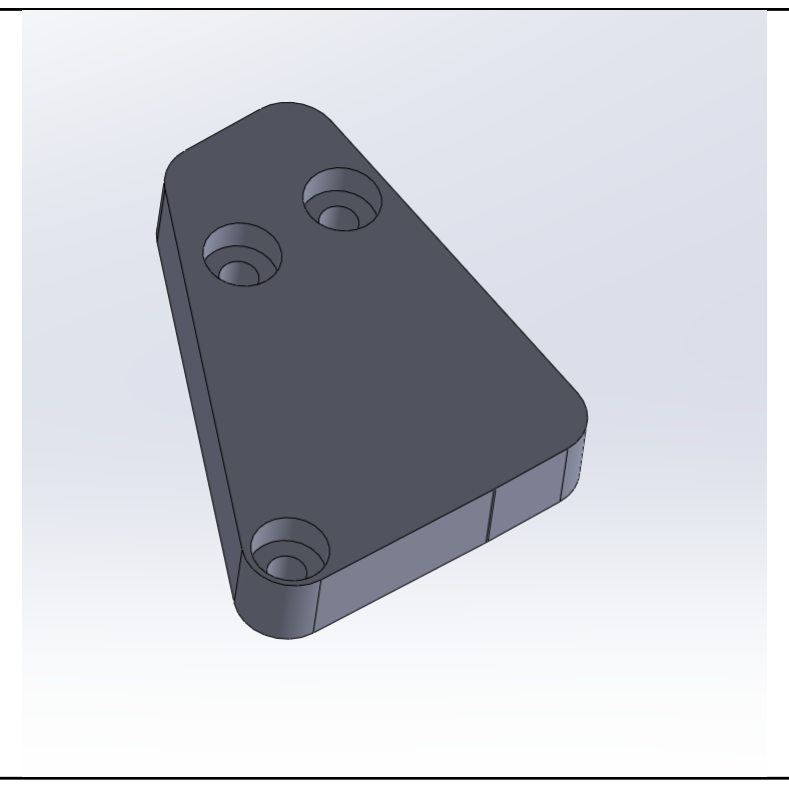
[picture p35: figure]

Elbow_blocker | 4.8 | honey | 25 | 0.15 | 6 | 5 | 3

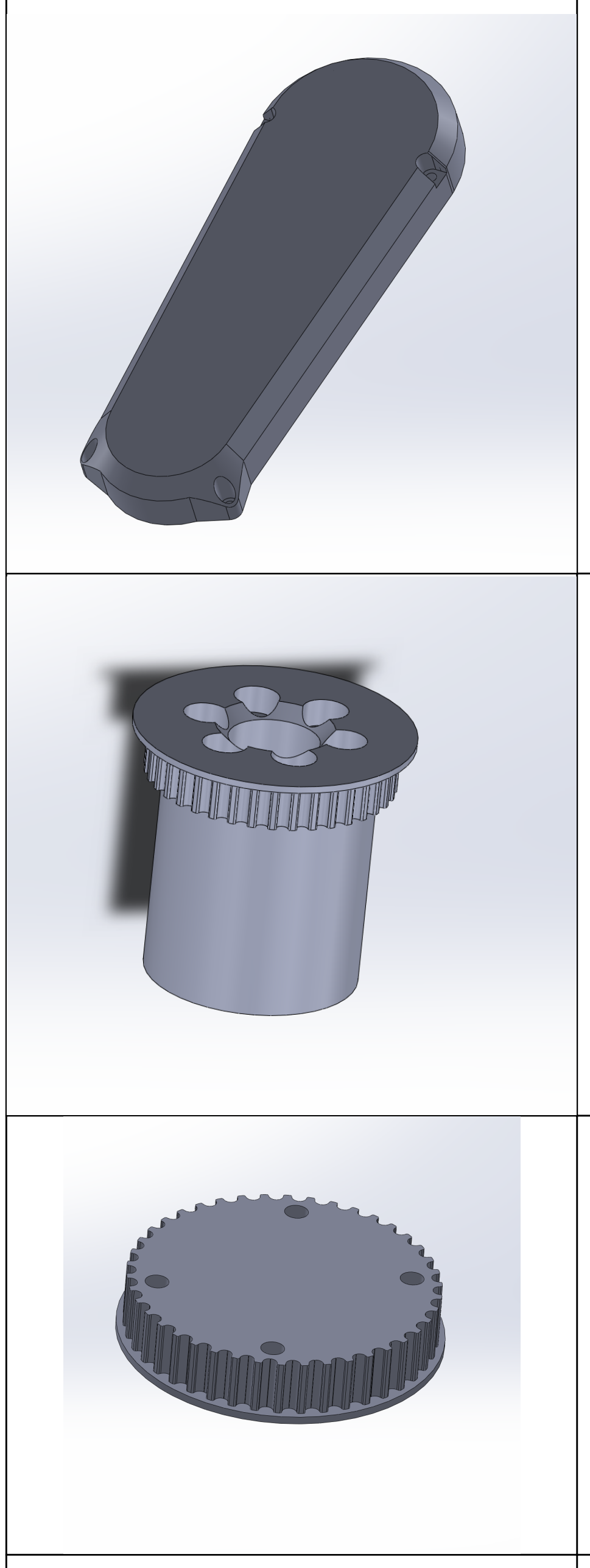
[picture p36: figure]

Upper_arm_cover | 26 | honey | 25 | 0.15 | 6 | 5 | 3
Upper_arm_pulley_38t | 22.3 | honey | 50 | 0.15 | 6 | 5 | 3
42_pulley | 8.5 | honey | 50 | 0.15 | 6 | 5 | 3

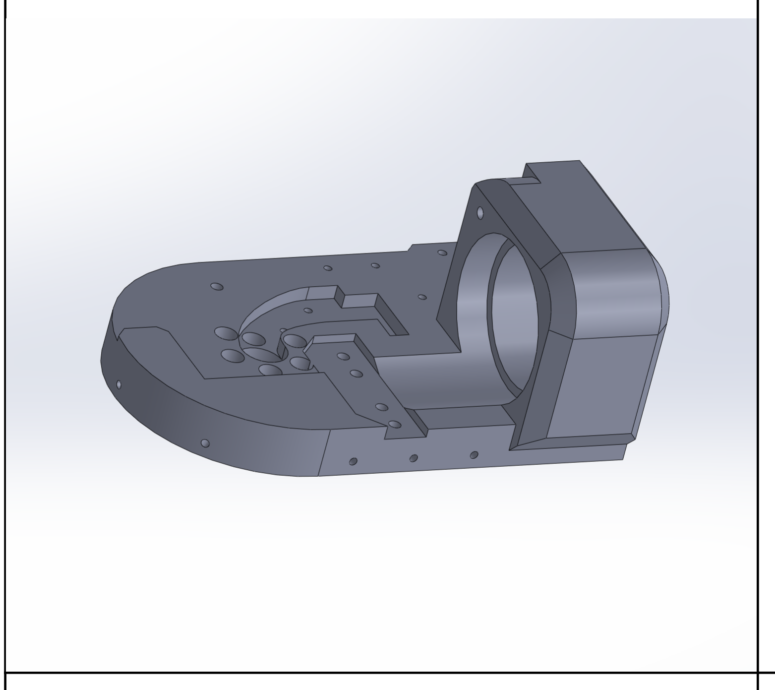
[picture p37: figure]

Turret | 179.1 | honey | 25 | 0.15 | 6 | 5 | 3

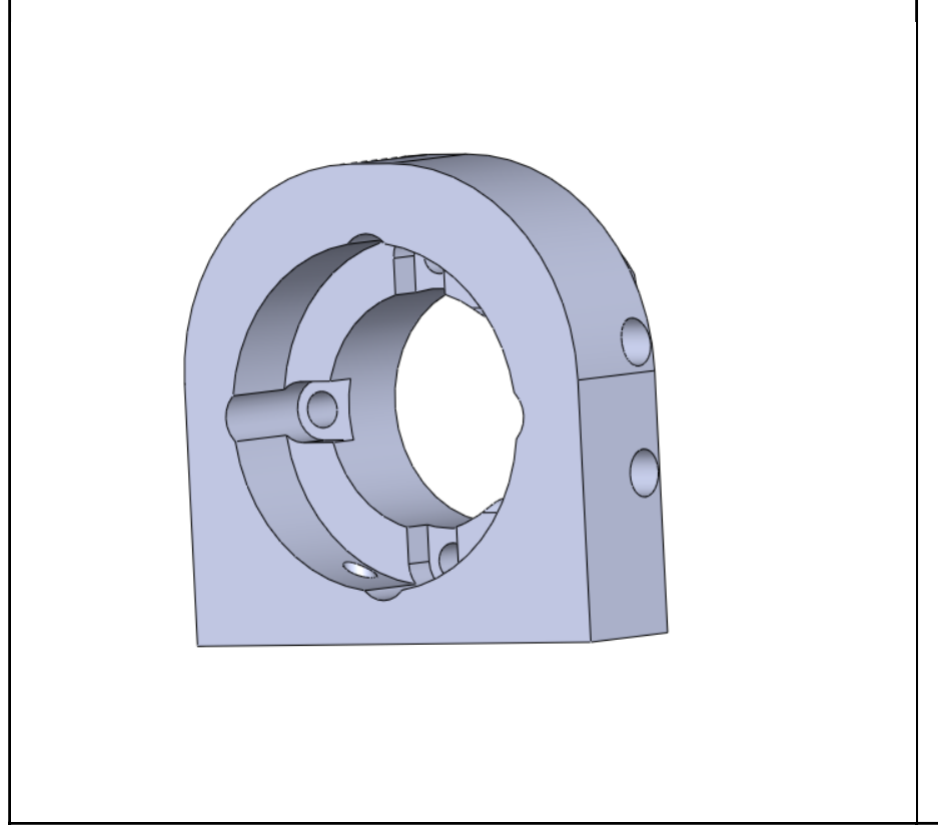
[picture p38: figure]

J2_turret_motor_holder | 33.8 | honey | 50 | 0.15 | 6 | 5 | 3

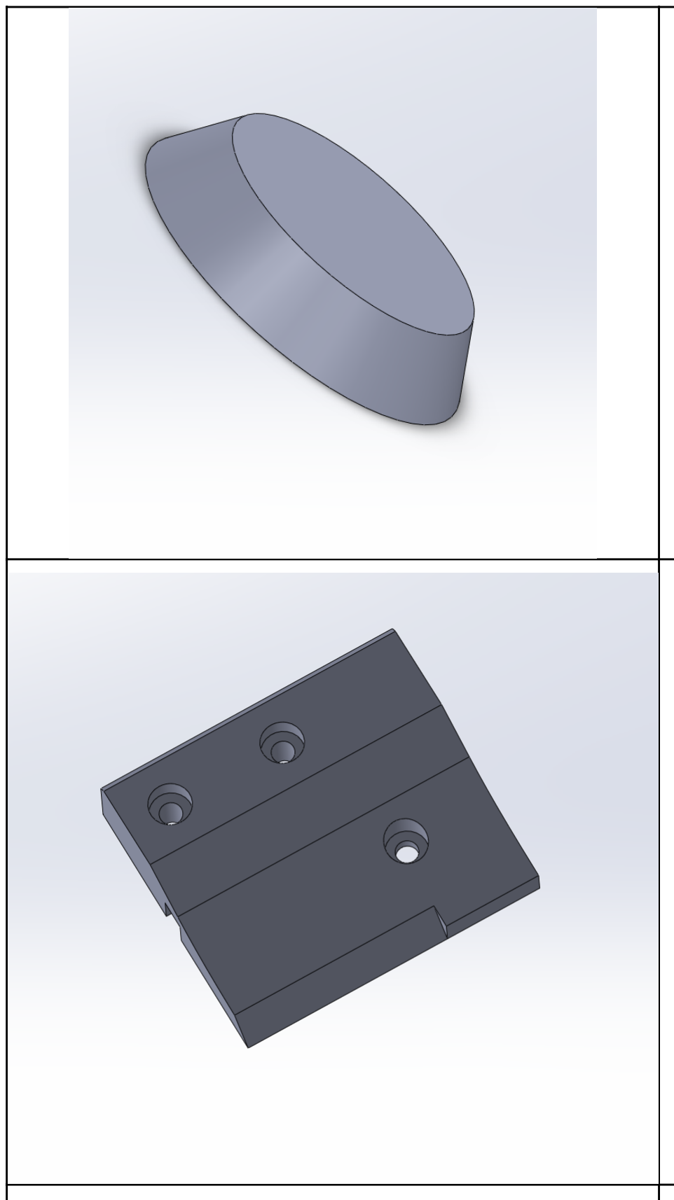
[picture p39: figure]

J2_cover | 11.1 | honey | 25 | 0.15 | 6 | 5 | 3
J2_blocker | 9.4 | honey | 25 | 0.15 | 6 | 5 | 3

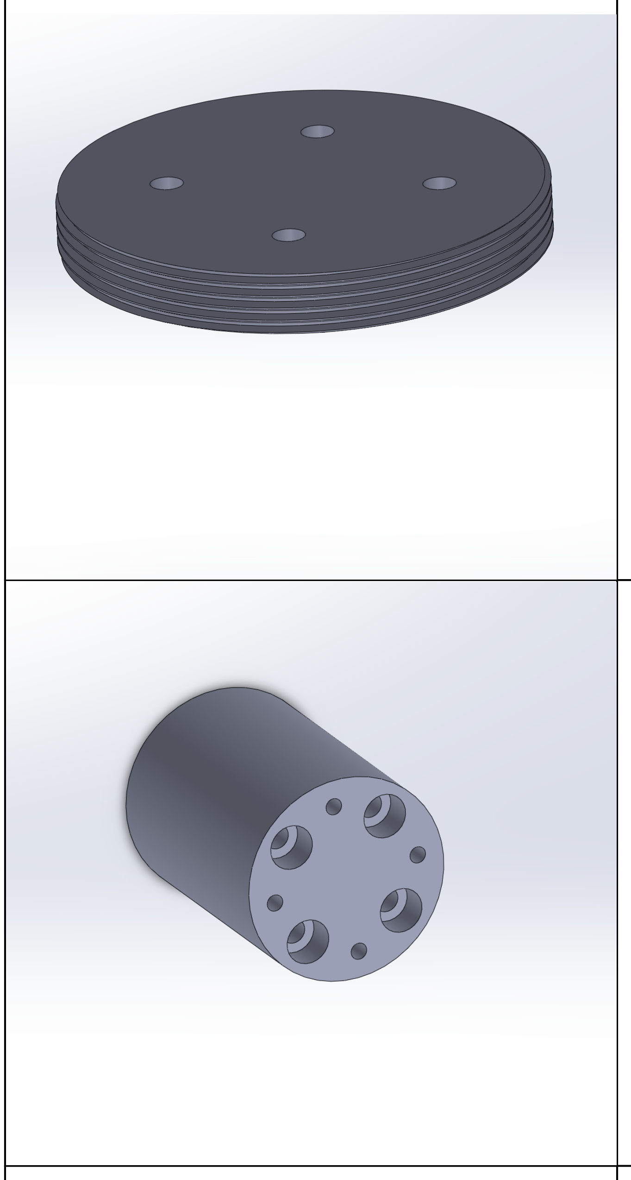
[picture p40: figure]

J2_bearing_backplate | 7 | honey | 25 | 0.15 | 6 | 5 | 3
J2_shaft | 37.4 | honey | 50 | 0.15 | 6 | 5 | 3

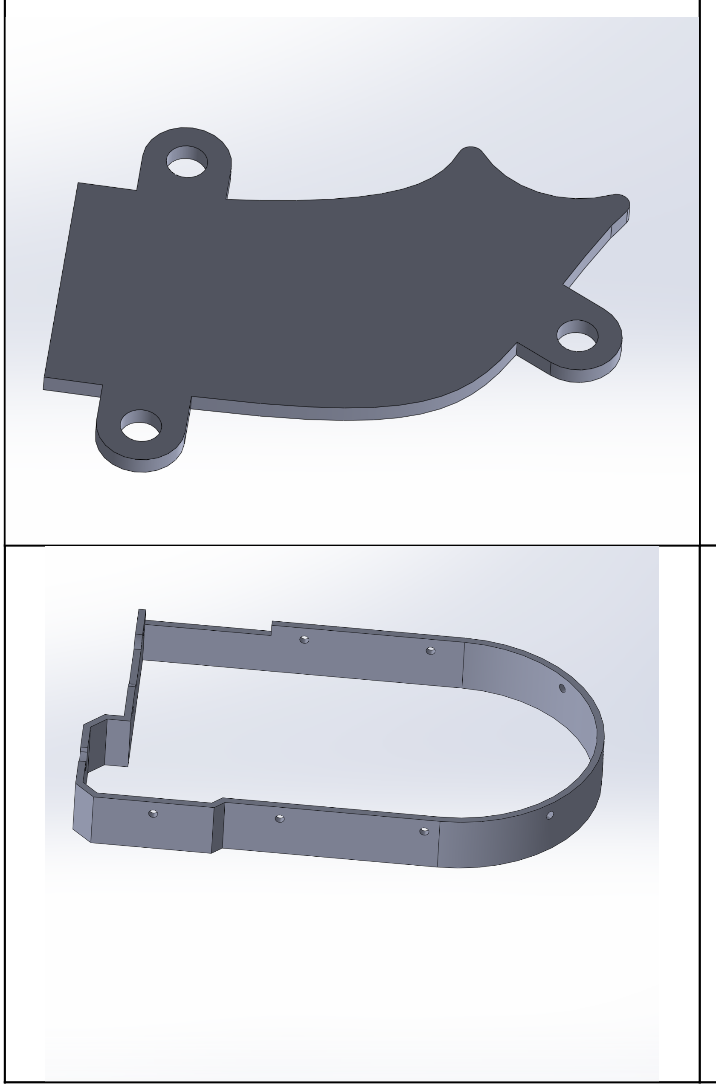
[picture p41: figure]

Turret_wire_cover | 1.7 | honey | 25 | 0.15 | 6 | 5 | 3
Turret_cover | 29 | honey | 25 | 0.15 | 6 | 5 | 3

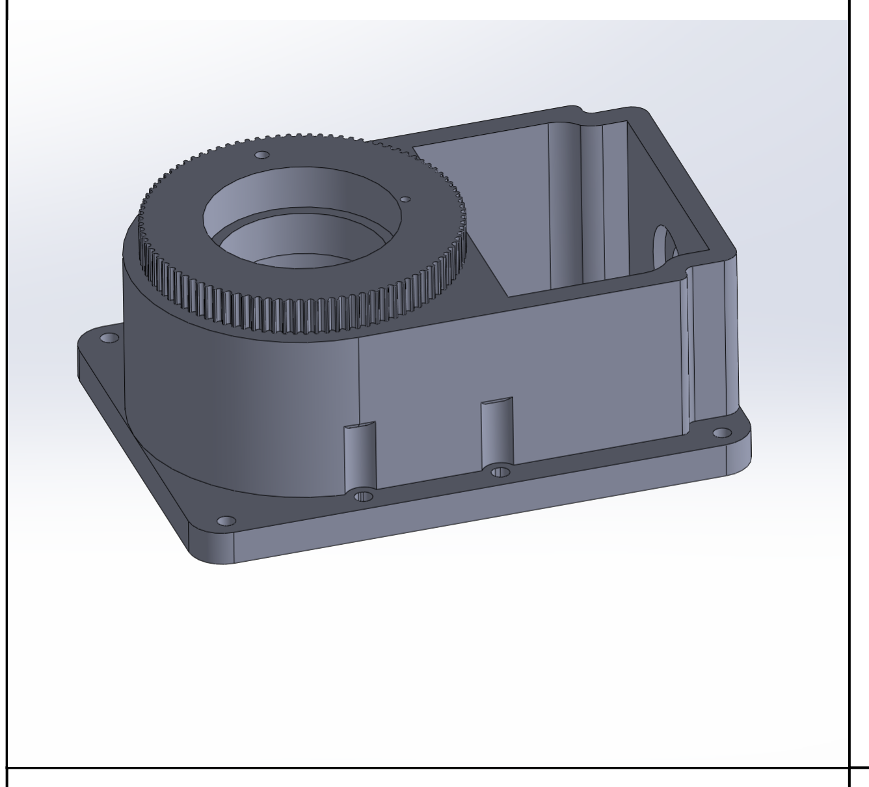
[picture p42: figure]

Base | 317 | honey | 25 | 0.15 | 6 | 5 | 3

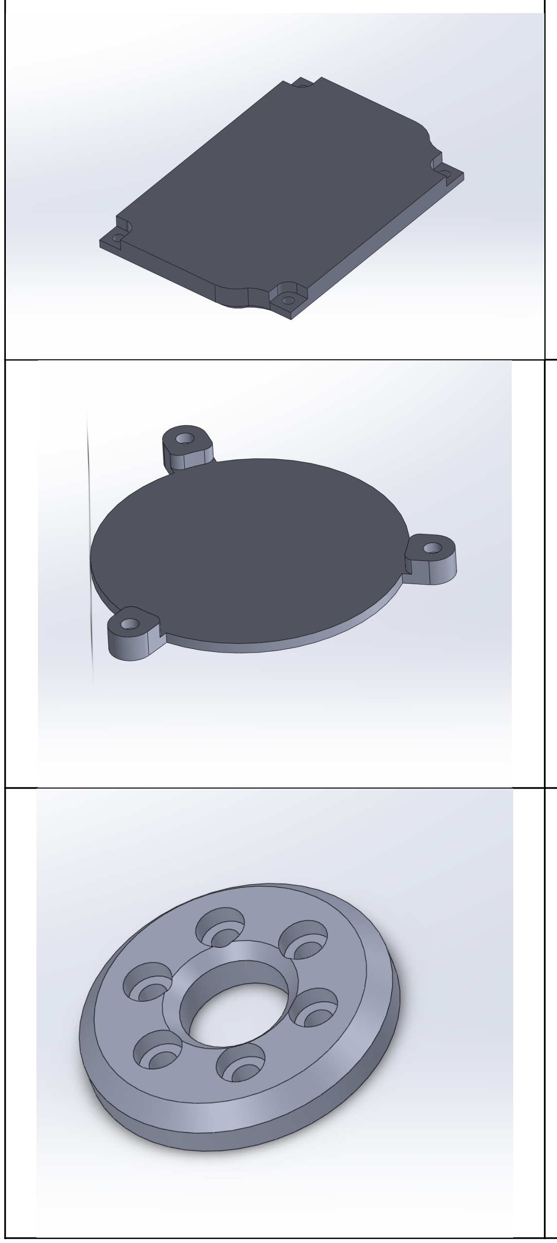
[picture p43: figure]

Base_lid_electronics | 35 | honey | 25 | 0.15 | 6 | 5 | 3
J1_bottom_lid | 6.1 | honey | 25 | 0.15 | 6 | 5 | 3
Base_bearing_backplate | 7.2 | honey | 25 | 0.15 | 6 | 5 | 3

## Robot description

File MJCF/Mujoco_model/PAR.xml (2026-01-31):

<!-- Reference for all paramteres -->
  <!--https://mujoco.readthedocs.io/en/stable/XMLreference.html-->
  <!-- File examples: -->
  <!-- https://github.com/google-deepmind/mujoco_menagerie/blob/main/trossen_vx300s/vx300s.xml -->
  <!-- https://github.com/google-deepmind/mujoco_menagerie/blob/main/aloha/aloha.xml -->
  <!-- https://github.com/google-deepmind/mujoco_menagerie/blob/main/franka_emika_panda/panda.xml -->
  <!-- https://github.com/jeongeun980906/lerobot-mujoco-tutorial/blob/master/asset/robotis_omy/omy.xml -->

<mujoco model="PAR6_URDF">
  <compiler angle="radian" autolimits="true"/>

  <option integrator="implicitfast"/>

  <!-- Default -->
  <default>
    <default class="Y">
      <joint range="-6.28319 6.28319" armature="0.001" damping="25.0" frictionloss="1.5"/>
      <position kp="500" forcerange="-300 300" ctrlrange="-6.28319 6.28319"/>
    </default>
    <default class="SSG48_gripper">
      <joint armature="0.1" damping="10.0" frictionloss="0"/>
      <position forcerange="-50 50" ctrlrange="-0.0235 0" kp="100"/>
    </default>
  </default>

  <asset>
    <mesh name="base_link" file="base_link.STL" scale="1 1 1"/>
    <mesh name="shoulder" file="shoulder.STL" scale="1 1 1"/>
    <mesh name="upper_arm" file="upper_arm.STL" scale="1 1 1"/>
    <mesh name="elbow" file="elbow.STL" scale="1 1 1"/>
    <mesh name="lower_arm" file="lower_arm.STL" scale="1 1 1"/>
    <mesh name="wrist" file="wrist.STL" scale="1 1 1"/>
    <mesh name="gripper" file="gripper.STL" scale="1 1 1"/>
    <mesh name="jaw1" file="jaw1.STL" scale="1 1 1"/>
    <mesh name="jaw2" file="jaw2.STL" scale="1 1 1"/>
  </asset>

  <worldbody>
    <geom type="mesh" rgba="0.79216 0.81961 0.93333 1" mesh="base_link"/>
    <body name="shoulder">
      <inertial pos="0.0065681 0.029094 0.099551" quat="0.438732 0.449118 -0.631911 0.454418" mass="1.993" diaginertia="0.00122723 0.00100741 0.000509712"/>
      <joint name="shoulder_JOINT" pos="0 0 0" axis="0 0 -1" class="Y"/>
      <geom type="mesh" rgba="0.75294 0.75294 0.75294 1" mesh="shoulder"/>
      <body name="upper_arm" pos="0.023421 0 0.1105" quat="0.707105 -0.707108 0 0">
        <inertial pos="-0.0085493 -0.071342 0.041639" quat="0.419414 0.451905 -0.587174 0.5245" mass="1.332" diaginertia="0.00165491 0.00161199 0.0002696"/>
        <joint name="upper_arm_JOINT" pos="0 0 0" axis="0 0 1" class="Y"/>
        <geom type="mesh" rgba="0.75294 0.75294 0.75294 1" mesh="upper_arm"/>
        <body name="elbow" pos="0 -0.18 0" quat="-2.59734e-06 0.707105 -0.707108 2.59735e-06">
          <inertial pos="0.015551 -0.019113 -0.0015332" quat="0.29143 0.634234 -0.265884 0.664922" mass="0.681" diaginertia="0.000816953 0.000689258 0.000454939"/>
          <joint name="elbow_JOINT" pos="0 0 0" axis="0 0 -1" class="Y"/>
          <geom type="mesh" rgba="0.75294 0.75294 0.75294 1" mesh="elbow"/>
          <body name="lower_arm" pos="0.0435 0 0" quat="-2.59734e-06 -2.59735e-06 -0.707108 -0.707105">
            <inertial pos="0.00052734 -0.010166 -0.092593" quat="0.959861 -0.262793 -0.0146171 -0.0969154" mass="0.579" diaginertia="0.000384758 0.000361865 0.000214287"/>
            <joint name="lower_arm_JOINT" pos="0 0 0" axis="0 0 -1" class="Y"/>
            <geom type="mesh" rgba="0.75294 0.75294 0.75294 1" mesh="lower_arm"/>
            <body name="wrist" pos="0 0 -0.177" quat="0.707105 -0.707108 0 0">
              <inertial pos="-1.5461e-06 -0.0031485 0.00019393" quat="0.721593 0.692318 0.000460117 -0.00048133" mass="0.523" diaginertia="0.00018083 0.000175719 0.000106091"/>
              <joint name="wrist_JOINT" pos="0 0 0" axis="0 0 1" class="Y"/>
              <geom type="mesh" rgba="0.79216 0.81961 0.93333 1" mesh="wrist"/>
              <body name="gripper" quat="0.707105 0.707108 0 0">
                <inertial pos="-6.7987e-05 0.0001694 -0.077391" quat="0.464161 0.46546 -0.535128 0.530603" mass="0.374" diaginertia="0.00014808 0.000127124 5.86313e-05"/>
                <joint name="gripper_JOINT" pos="0 0 0" axis="0 0 -1" class="Y"/>
                <geom type="mesh" rgba="0.79216 0.81961 0.93333 1" mesh="gripper"/>
                            <!-- Camera center -->
                <body name="camera_center" pos="0.0 -0.09 0.1">
                    <geom size="0.005 0.005 0.005" pos="0. 0. 0." contype="0" conaffinity="0" type="box" rgba="1.00 0.00 0.0 0" />
                    <camera name="egocentric" pos="0 0 0" xyaxes="-1 0 0 0 0 1" fovy="90" />
                </body>

                <body name="tcp_link" pos="0 -0.22 0">
                  <geom type="capsule" fromto="0 0 -0.5 0 0 0.5" size="0.01" rgba="1.0 0.2 0.2 0.0" contype="0" conaffinity="0"/>
                </body>

                <body name="jaw1" pos="0 0 -0.11745" quat="1.34924e-11 3.67321e-06 1 3.67321e-06">
                  <inertial pos="0.0033269 0.029197 -0.0097237" quat="0.427918 0.661892 -0.405093 0.463342" mass="0.02" diaginertia="4.64011e-06 3.93984e-06 1.21885e-06"/>
                  <joint name="jaw1_JOINT" pos="0 0 0" axis="0 -1 0" type="slide" range="-0.0235 0" class="SSG48_gripper"/>
                  <geom type="mesh" rgba="0.29804 0.29804 0.29804 1" mesh="jaw1"/>
                </body>

                <body name="jaw2" pos="0 0 -0.11745" quat="1.34924e-11 3.67321e-06 1 3.67321e-06">
                  <inertial pos="-0.0033269 -0.029197 -0.0097237" quat="0.405093 0.463342 -0.427918 0.661892" mass="0.02" diaginertia="4.64011e-06 3.93984e-06 1.21885e-06"/>
                  <joint name="jaw2_JOINT" pos="0 0 0" axis="0 -1 0" type="slide" range="0 0.0235" class="SSG48_gripper"/>
                  <geom type="mesh" rgba="0.29804 0.29804 0.29804 1" mesh="jaw2"/>
                </body>  
                
              </body>
            </body>
          </body>
        </body>
      </body>
    </body>
  </worldbody>


  <!-- Exclude contact information -->
  <contact>
    <exclude body1="world" body2="shoulder"/>
  </contact>

  <!-- Gripper fingers are parallel -->
  <equality>
    <joint joint1="jaw2_JOINT" joint2="jaw1_JOINT" polycoef="0 -1 0 0 0"/>
  </equality>

  <!-- Define actuators -->
  <actuator>
    <position name="actuator_joint1" joint="shoulder_JOINT" class="Y"/>
    <position name="actuator_joint2" joint="upper_arm_JOINT" class="Y"/>
    <position name="actuator_joint3" joint="elbow_JOINT" class="Y"/>
    <position name="actuator_joint4" joint="lower_arm_JOINT" class="Y"/>
    <position name="actuator_joint5" joint="wrist_JOINT" class="Y"/>
    <position name="actuator_joint6" joint="gripper_JOINT" class="Y"/>

    <position name="actuator_rh_r1" joint="jaw1_JOINT" class="SSG48_gripper"/>


  </actuator>

</mujoco>

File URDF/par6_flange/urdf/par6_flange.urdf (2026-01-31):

<?xml version="1.0" encoding="utf-8"?>
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
<robot name="par6_flange">
  <link name="base_link">
    <inertial>
      <origin xyz="-0.03291842362796 -3.9760226777652E-09 0.0314011608034117" rpy="0 0 0" />
      <mass value="0.998265338800333" />
      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
    </inertial>
    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
  </link>
  <link name="shoulder">
    <inertial>
      <origin xyz="0.00656811939881225 0.029093538967332 0.099551347543143" rpy="0 0 0" />
      <mass value="0.620900499130961" />
      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
    </inertial>
    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
  </link>
  <joint name="shoulder_JOINT" type="revolute">
    <origin xyz="0 0 0" rpy="0 0 0" />
    <parent link="base_link" />
    <child link="shoulder" />
    <axis xyz="0 0 -1" />
    <limit lower="0" upper="0" effort="0" velocity="0" />
  </joint>
  <link name="upper_arm">
    <inertial>
      <origin xyz="-0.00854934366236464 -0.071342142449425 0.0416391335881913" rpy="0 0 0" />
      <mass value="0.564255649327409" />
      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
    </inertial>
    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
  </link>
  <joint name="upper_arm_JOINT" type="revolute">
    <origin xyz="0.0234207210610365 0 0.1105" rpy="-1.5707963267949 0 0" />
    <parent link="shoulder" />
    <child link="upper_arm" />
    <axis xyz="0 0 1" />
    <limit lower="0" upper="0" effort="0" velocity="0" />
  </joint>
  <link name="elbow">
    <inertial>
      <origin xyz="0.0155509885239581 -0.0191127686426632 -0.00153322577917242" rpy="0 0 0" />
      <mass value="0.550970997806044" />
      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
    </inertial>
    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
  </link>
  <joint name="elbow_JOINT" type="revolute">
    <origin xyz="0 -0.18 0" rpy="3.14159265358979 0 -1.5707963267949" />
    <parent link="upper_arm" />
    <child link="elbow" />
    <axis xyz="0 0 -1" />
    <limit lower="0" upper="0" effort="0" velocity="0" />
  </joint>
  <link name="lower_arm">
    <inertial>
      <origin xyz="0.00052733545462913 -0.0101658497051341 -0.0925926618710992" rpy="0 0 0" />
      <mass value="0.382768168076153" />
      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
    </inertial>
    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
  </link>
  <joint name="lower_arm_JOINT" type="revolute">
    <origin xyz="0.0434999999999984 0 0" rpy="1.5707963267949 0 -3.14159265358979" />
    <parent link="elbow" />
    <child link="lower_arm" />
    <axis xyz="0 0 -1" />
    <limit lower="0" upper="0" effort="0" velocity="0" />
  </joint>
  <link name="wrist">
    <inertial>
      <origin xyz="-1.54606600299978E-06 -0.00314847566621396 0.000193929742576593" rpy="0 0 0" />
      <mass value="0.230864625594321" />
      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
    </inertial>
    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
  </link>
  <joint name="wrist_JOINT" type="revolute">
    <origin xyz="0 0 -0.177000000000002" rpy="-1.57079632679489 0 0" />
    <parent link="lower_arm" />
    <child link="wrist" />
    <axis xyz="0 0 1" />
    <limit lower="0" upper="0" effort="0" velocity="0" />
  </joint>
  <link name="gripper">
    <inertial>
      <origin xyz="-6.28287090892465E-05 6.96476392843537E-05 -0.0490534784184994" rpy="0 0 0" />
      <mass value="0.024635742513522" />
      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
    </inertial>
    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
  </link>
  <joint name="gripper_JOINT" type="revolute">
    <origin xyz="0 0 0" rpy="1.5707963267949 0 0" />
    <parent link="wrist" />
    <child link="gripper" />
    <axis xyz="0 0 -1" />
    <limit lower="0" upper="0" effort="0" velocity="0" />
  </joint>
</robot>

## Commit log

2026-01-31 Initial commit with STL files and URDF files
    [42_pulley_old.STL, Elbow_lid.STL, J1_backplate.STL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]
2026-02-04 add reference images
    [42_pulley_old.STL, Base_bearing_backplate.STL, Cable_tie_mount.STL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]
2026-04-02 Added digrams for wiring
2026-04-10 update steps
    [Stepper_spacer_J6.STL, Stepper_spacer_NEMA17.STEP]
2026-04-17 update cable tie mounts
    [Cable_tie_mount.STL]
2026-05-03 add gearbox extenders
    [MG_series_gaerbox_extender_20_1.STEP, MG_series_gaerbox_extender_20_1.STL, MG_series_gearbox_extender_10_1.STL]
2026-05-03 Update assembly manual
2026-05-03 Update BOM with new gearbox and bearing quantities

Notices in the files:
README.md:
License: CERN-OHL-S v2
